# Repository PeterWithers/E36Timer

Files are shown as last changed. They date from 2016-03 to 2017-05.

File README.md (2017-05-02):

# E36Timer
Simple and cheep free flight timer

This timer is based on the attiny86 usb board. These boards usually ship with the micronucleus boot loader, in which case it can be flashed with the command line tool: micronucleus --run e36timer.hex

The components required for this are: attiny86 usb board, push button and wiring for the button, servo and ESC.

When the device is powered up there will be a period of time in which the motor run time and DT time can be adjusted. The options will be: 
Motor times: 5, 10, 15 seconds
DT time: 0, 5, 30, 60, 90, 120, 180, 240, 300 seconds

It is possible that powersupply noise or interruptions could cause the attiny to brownout. For this reason the first action on power up should be to release the DT, otherwise a brownout mid flight could prevent or delay DT.

The main working branch for this project is now on GITLAB during the current stage of development.

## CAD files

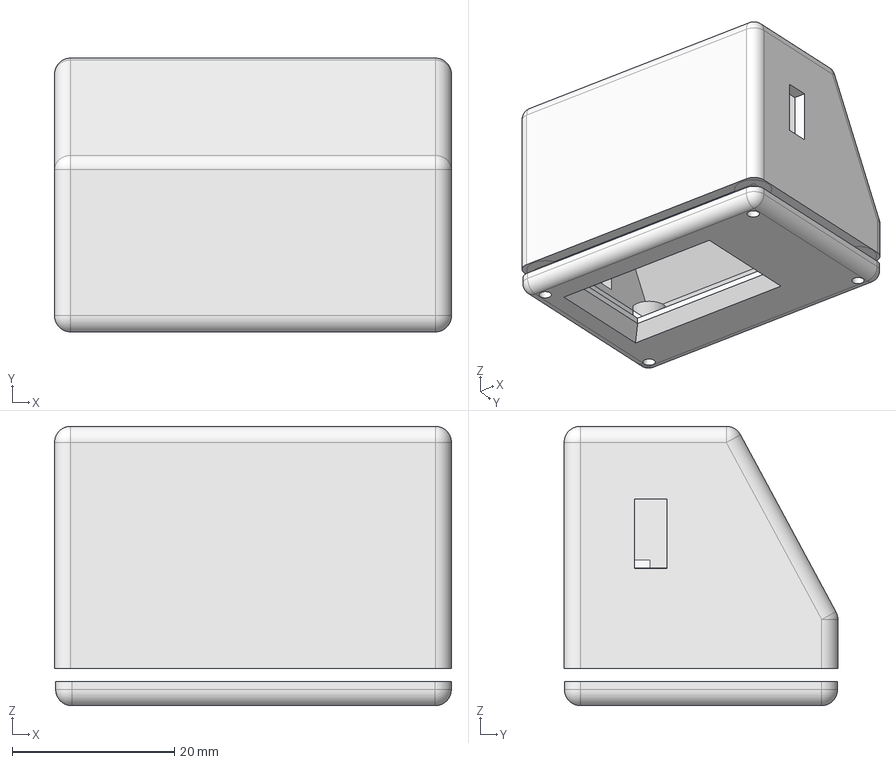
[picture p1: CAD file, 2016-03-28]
timer_testing_tool/testing_tool_case.FCStd
49.0 x 33.8 x 34.5 mm
LCD
Board
USB
Connector

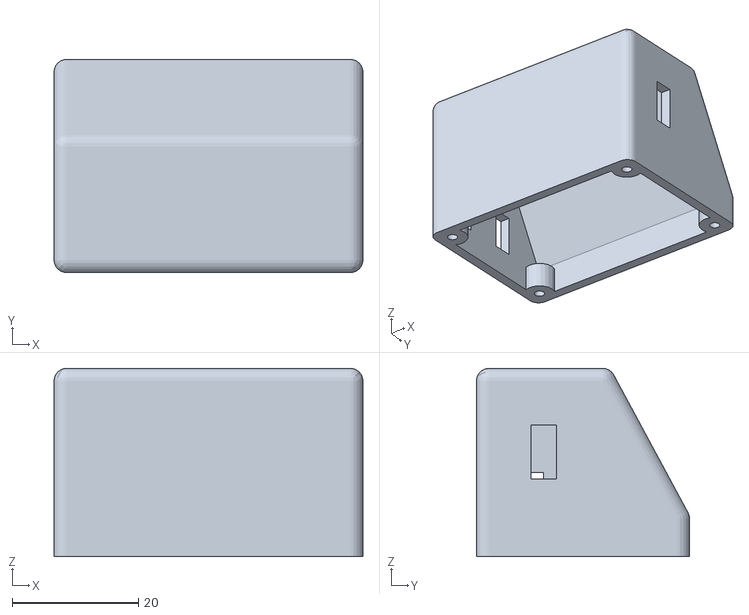
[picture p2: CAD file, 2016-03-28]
timer_testing_tool/case_body.stl
49.0 x 33.8 x 29.9

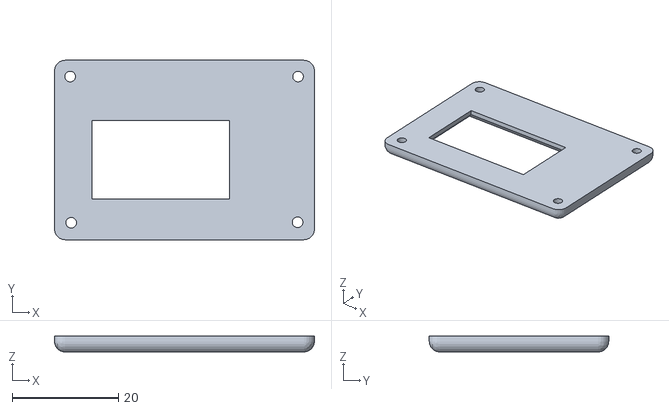
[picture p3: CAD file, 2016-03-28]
timer_testing_tool/face_plate.stl
48.8 x 33.7 x 3.00

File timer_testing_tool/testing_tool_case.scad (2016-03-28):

/*
 * Copyright (C) 2016 Peter Withers
 */

/*
 * testing_tool_case.scad
 *
 * Created: 21/03/2016 23:18
 * Author : Peter Withers <peter@gthb-bambooradical.com>
 */

lcdHoleSpacing = 23;
lcdBoardWidth = 28; // the board is square
lcdDisplayHeight = 18; // the lcd is as wide as the board

atmegaBoardWidth = 18;
atmegaBoardLength = 43;

gapBetweenBoardEdgeAndLcd = 5;

usbWidth = 8;
usbHeight = 4;

//translate([0,5,5]) %cube([atmegaBoardLength, 30, lcdBoardWidth+5], center = true);
//cube([atmegaBoardLength, atmegaBoardWidth, 3], center = true);
//translate([-5,18,5]) cube([lcdBoardWidth, 3, lcdBoardWidth], center = true);
//translate([-5,20,4]) cube([lcdBoardWidth, 5, lcdDisplayHeight], center = true);
//translate([25,0,-3]) cube([usbWidth, usbWidth, usbHeight], center = true);
//translate([-25,0,-3]) rotate(90, [0,1,0]) cylinder(r = 3, h = 10, center = true);

difference() {
	// facePlate
	translate([0,22,5]) cube([atmegaBoardLength+ 5, 3, lcdBoardWidth+5], center = true);
	// LCD hole
	translate([-5,20,4]) cube([lcdBoardWidth, 15, lcdDisplayHeight], center = true);
	rotate(90, [0,1,0]) translate([-5,20,4]) cylinder(r=1,h=30, center = true);
	
}

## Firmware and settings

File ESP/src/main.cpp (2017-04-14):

/*
 * Copyright (C) 2016 Peter Withers
 */

/*
 * E36Timer.c
 *
 * Created: 13/02/2016 18:00:32
 * Author : Peter Withers <peter@gthb-bambooradical.com>
 */

//#include <Arduino.h>
//#include <eeprom.h>
#include <EEPROM.h>
#include <Servo.h>
// todo: this include and related defines are temporary
//#include <NewPing.h>
#include <user_interface.h>
#include <ESP8266WiFi.h>
#include <DNSServer.h>
#include <ESP8266WebServer.h>
#include <ESP8266HTTPUpdateServer.h>
#include <Sodaq_BMP085.h>
#include <Wire.h>
#include <Ticker.h>

Ticker pwmTweenTimer;
ADC_MODE(ADC_VCC);
WiFiUDP Udp;
unsigned int localUdpPort = 2222;

const byte DNS_PORT = 53;
IPAddress timerIP(192, 168, 1, 1);
IPAddress remoteIP(192, 168, 1, 2);
DNSServer dnsServer;
ESP8266WebServer webServer(80);
ESP8266HTTPUpdateServer httpUpdater;

Sodaq_BMP085 pressureSensor;
double baselinePressure;
bool isTimer = false;
bool hasPressureSensor = true;

int historyLength = 1024;
int historyIndex = 0;
int udpHistoryIndex = 0;
int flightStartIndex = 0;
float temperatureHistory[1024];
float altitudeHistory[1024];
uint8_t escHistory[1024];
uint8_t dtHistory[1024];
int32_t remoteRssiHistory[1024];
float remoteVoltageHistory[1024];
int maxSvgValue = 0;

//#define TRIGGER_PIN  3
//#define ECHO_PIN     2
//#define MAX_DISTANCE 400

//NewPing sonar(TRIGGER_PIN, ECHO_PIN, MAX_DISTANCE);
// end temporary defines

#define IndicatorLed     2
#define ServoPWM         4
#define EscPWM           5
#define ButtonPin        0
#define SdaPin           12
#define SclPin           14

Servo dtServo;
Servo escServo;

#define MaxPwm 141
#define MinPwm 44

//#define ButtonIsDown (sonar.ping_cm() < 30)
#define ButtonIsDown (digitalRead(ButtonPin) == 0)
#define RcDtIsActive false
//#define RcDtIsActive (digitalRead(RcDt1Pin) == 0)

#define TurnOnLed digitalWrite(IndicatorLed, 1)
#define TurnOffLed digitalWrite(IndicatorLed, 0)

typedef union {

    struct {
        uint8_t dtStatus;
        int32_t rssi;
        uint16_t voltage;
    } data;
    uint8_t asBytes[sizeof (data)];
} TelemetryData;

enum MachineState {
    setupSystem,
    throttleMax,
    waitingButtonRelease1,
    throttleMin,
    waitingButtonRelease2,
    startWipe1, // when the device resets we wipe the servo arm to release the DT lever so that a reset in midair does not prevent DT
    endWipe1,
    editMotorTime,
    startWipe2, // between the settings wipe to indicate the change
    endWipe2,
    editDtTime,
    saveEepromSettings,
    waitingButtonStart,
    clearGraphArrays,
    waitingButtonRelease,
    motorRun,
    freeFlight,
    triggerDT,
    waitingForRestart,
    waitingFirmwareUpdate,
    dtRemoteConfig,
    dtRemote
};

volatile enum MachineState machineState = setupSystem;

volatile unsigned long buttonLastChangeMs = 0;
volatile unsigned long buttonDebounceMs = 100;

volatile unsigned long lastMotorSpinUpMs = 0;
volatile unsigned long flightIdRandom1 = 0;
volatile unsigned long flightIdRandom2 = 0;
volatile unsigned long currentFlightMs = 0;
volatile unsigned long lastStateChangeMs = 0;
volatile const unsigned long editingTimeoutMs = 3000;
volatile const unsigned long escSpinDownMs = 1000;
volatile const unsigned long escSpinUpMs = 1000;
volatile const unsigned long servoWipeMs = 1000;
volatile const unsigned long displayStepMs = 500;
volatile unsigned long editingStartMs = 0;
volatile const unsigned long powerDownServoMs = 30l * 1000l; // 30 seconds before the servo is powered down
volatile const unsigned long powerDownEscSeconds = 300l * 1000l; // 5 minutes before the ESC is powered down

const unsigned long motorSeconds[] = {2, 4, 5, 7, 10, 13, 15};
const int motorSecondsSize = 6;
volatile int motorSecondsIndex = 0;
const unsigned long dethermalSeconds[] = {0, 5, 30, 60, 90, 120, 180, 240, 300};

// start measured actual times
// tested with the timer calibrated to produce 50.38hz
// motor 2: {2.3}
// motor 7: {7.2}
// motor 15: {14.9,14.6,14.9,14.7};
// any DT below motor time of 15: {16.0,15.7}
// DT 0 with motor 2: {3.4}
// DT 30: {30.6};
// DT 60: {59.8};
// DT 300: {293.0};
// end measured actual times

const int dethermalSecondsSize = 9;
volatile int dethermalSecondsIndex = 0;
const int waitingEscValue = ((MaxPwm - MinPwm) / 3) + MinPwm;
volatile int buttonHasBeenUp = 0;

char ssid[32] = "";
char password[32] = "";

void slowFlash() {
    if (millis() / 1000 % 2 == 0) {
        TurnOnLed;
    } else {
        TurnOffLed;
    }
}

void fastFlash() {
    if ((millis() / (1000 / 5)) % 2 == 0) {
        TurnOnLed;
    } else {
        TurnOffLed;
    }
}

void doubleFlash() {
    int pulseIndex = (millis() / (1000 / 5)) % 10;
    if (pulseIndex == 0 || pulseIndex == 3) {
        TurnOnLed;
    } else {
        TurnOffLed;
    }
}

void trippleFlash() {
    int pulseIndex = (millis() / (1000 / 5)) % 10;
    if (pulseIndex == 0 || pulseIndex == 2 || pulseIndex == 4) {
        TurnOnLed;
    } else {
        TurnOffLed;
    }
}

void setCredentials() {
    if (webServer.hasArg("ssid") && webServer.hasArg("pass")) {
        webServer.arg("ssid").toCharArray(ssid, sizeof (ssid) - 1);
        webServer.arg("pass").toCharArray(password, sizeof (password) - 1);
        EEPROM.begin(512);
        EEPROM.put(9, ssid);
        EEPROM.put(9 + sizeof (ssid), password);
        char ok[2 + 1] = "OK";
        EEPROM.put(9 + sizeof (ssid) + sizeof (password), ok);
        EEPROM.commit();
        EEPROM.end();
    }
}

void saveSettings() {
    boolean changeMade = false;
    EEPROM.begin(512);
    Serial.print(" motorSecondsIndex: ");
    Serial.print(motorSecondsIndex);
    Serial.print(" EEPROM.read(1): ");
    Serial.print(EEPROM.read(1));
    // using update not write to preserve eeprom life
    // update does not seem to exist in the ESP library so we test before setting to preserve the eeprom
    if (EEPROM.read(1) != motorSecondsIndex) {
        Serial.print(" motorSecondsIndex storing changes");
        EEPROM.write(1, motorSecondsIndex);
        changeMade = true;
    } else {
        Serial.print(" motorSecondsIndex unchanged");
    }
    if (EEPROM.read(2) != dethermalSecondsIndex) {
        Serial.print(" dethermalSecondsIndex storing changes");
        EEPROM.write(2, dethermalSecondsIndex);
        changeMade = true;
    } else {
        Serial.print(" dethermalSecondsIndex unchanged");
    }
    byte settingsByte = EEPROM.read(3);
    if (bitRead(settingsByte, 0) != isTimer || bitRead(settingsByte, 1) != hasPressureSensor) {
        Serial.print(" toggleTimerOrRemote, hasPressureSensor storing changes");
        bitWrite(settingsByte, 0, isTimer);
        bitWrite(settingsByte, 1, hasPressureSensor);
        EEPROM.write(3, settingsByte);
        changeMade = true;
    } else {
        Serial.print(" toggleTimerOrRemote, hasPressureSensor unchanged");
    }
    if (changeMade) {
        Serial.print(" writing changes");
        EEPROM.commit();
    } else {
        Serial.print(" unchanged no commit");
    }
    EEPROM.end();
}

void loadSavedSettings() {
    EEPROM.begin(512);
    motorSecondsIndex = EEPROM.read(1);
    dethermalSecondsIndex = EEPROM.read(2);
    byte settingsByte = EEPROM.read(3);
    isTimer = bitRead(settingsByte, 0);
    hasPressureSensor = bitRead(settingsByte, 1);
    motorSecondsIndex = (motorSecondsIndex < motorSecondsSize) ? motorSecondsIndex : motorSecondsSize - 1;
    dethermalSecondsIndex = (dethermalSecondsIndex < dethermalSecondsSize) ? dethermalSecondsIndex : dethermalSecondsSize - 1;
    EEPROM.get(9, ssid);
    EEPROM.get(9 + sizeof (ssid), password);
    char ok[2 + 1];
    EEPROM.get(9 + sizeof (ssid) + sizeof (password), ok);
    if (String(ok) != String("OK")) {
        ssid[0] = 0;
        password[0] = 0;
    }
    EEPROM.end();
}

void pinChangeInterrupt() {
    buttonLastChangeMs = millis();
}

String getTelemetryJson() {
    String returnString = "machineState: '";
    switch (machineState) {
        case setupSystem:
            returnString += "setupSystem";
            break;
        case throttleMax:
            returnString += "throttleMax";
            break;
        case waitingButtonRelease1:
            returnString += "waitingButtonRelease1";
            break;
        case throttleMin:
            returnString += "throttleMin";
            break;
        case waitingButtonRelease2:
            returnString += "waitingButtonRelease2";
            break;
        case startWipe1:
            returnString += "startWipe1";
            break;
        case endWipe1:
            returnString += "endWipe1";
            break;
        case editMotorTime:
            returnString += "editMotorTime";
            break;
        case startWipe2:
            returnString += "startWipe2";
            break;
        case endWipe2:
            returnString += "endWipe2";
            break;
        case editDtTime:
            returnString += "editDtTime";
            break;
        case saveEepromSettings:
            returnString += "saveEepromSettings";
            break;
        case waitingButtonStart:
            returnString += "waitingButtonStart";
            break;
        case clearGraphArrays:
            returnString += "clearGraphArrays";
            break;
        case waitingButtonRelease:
            returnString += "waitingButtonRelease";
            break;
        case motorRun:
            returnString += "motorRun";
            break;
        case freeFlight:
            returnString += "freeFlight";
            break;
        case triggerDT:
            returnString += "triggerDT";
            break;
        case waitingForRestart:
            returnString += "waitingForRestart";
            break;
        case waitingFirmwareUpdate:
            returnString += "waitingFirmwareUpdate";
            break;
        case dtRemoteConfig:
            returnString += "dtRemoteConfig";
            break;
        case dtRemote:
            returnString += "dtRemote";
            break;
    }
    int servoPosition = dtServo.read();
    int escPosition = escServo.read();
    returnString += "'; servoPosition: ";
    returnString += servoPosition;
    returnString += "; escPosition: ";
    returnString += escPosition;
    returnString += "; dethermalSeconds: ";
    returnString += dethermalSeconds[dethermalSecondsIndex];
    returnString += "; motorSeconds: ";
    returnString += motorSeconds[motorSecondsIndex];
    returnString += "; rssi: ";
    returnString += WiFi.RSSI();
    returnString += "; lastStateChangeMs: ";
    returnString += (millis() - lastStateChangeMs);
    return returnString;
}

bool getPressure(double &temperature, double &pressure, double &altitude) {
    temperature = pressureSensor.readTemperature();
    pressure = pressureSensor.readPressure();
    altitude = pressureSensor.readAltitude(baselinePressure);

    /*Serial.print("altitudeHistory: ");
    for (int currentIndex = 0; currentIndex < historyLength; currentIndex++) {
        Serial.print(altitudeHistory[currentIndex]);
        Serial.print(", ");
    }
    Serial.println(";");
    Serial.print("temperatureHistory: ");
    for (int currentIndex = 0; currentIndex < historyLength; currentIndex++) {
        Serial.print(temperatureHistory[currentIndex]);
        Serial.print(", ");
    }
    Serial.println(";");*/
    return true;
}
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
void loop() {
    switch (machineState) {
        case saveEepromSettings:
            saveSettings();
            machineState = waitingButtonStart;
            break;
        case clearGraphArrays:
            machineState = waitingButtonRelease;
            // zero the historyIndex and zero the history buffer
            lastMotorSpinUpMs = millis();
            flightIdRandom1 = random(1000, 9999); // @todo: the random seed has not been set, check that this will not cause issues in this use case.
            flightIdRandom2 = random(1000, 9999);
            memset(temperatureHistory, 0, sizeof (temperatureHistory));
            memset(altitudeHistory, 0, sizeof (altitudeHistory));
            memset(escHistory, 0, sizeof (escHistory));
            memset(dtHistory, 0, sizeof (dtHistory));
            memset(remoteRssiHistory, 0, sizeof (remoteRssiHistory));
            memset(remoteVoltageHistory, 0, sizeof (remoteVoltageHistory));
            break;
        case dtRemoteConfig:
            if (WiFi.status() == WL_CONNECTED) {
                dnsServer.stop();
                webServer.stop();
                WiFi.softAPdisconnect(true);
                WiFi.mode(WIFI_STA);
                machineState = dtRemote;
            }
            break;
        case dtRemote:
            TelemetryData telemetryData;
            if (ButtonIsDown) {
                telemetryData.data.dtStatus = 'd';
                Udp.beginPacket(timerIP, localUdpPort);
                Udp.write(telemetryData.asBytes, sizeof (telemetryData));
                Udp.endPacket();
            } else {
                int currentIndex = ((millis() - lastMotorSpinUpMs) / 1000);
                if (currentIndex != udpHistoryIndex) {
                    telemetryData.data.dtStatus = 'r';
                    telemetryData.data.rssi = WiFi.RSSI();
                    telemetryData.data.voltage = ESP.getVcc();
                    //                    Serial.print("rssi: ");
                    //                    Serial.println(telemetryData.data.rssi);
                    //                    Serial.print("voltage: ");
                    //                    Serial.println(telemetryData.data.voltage);
                    udpHistoryIndex = currentIndex;
                    Udp.beginPacket(timerIP, localUdpPort);
                    Udp.write(telemetryData.asBytes, sizeof (telemetryData));
                    Udp.endPacket();
                }
            }
            int packetSize = Udp.parsePacket();
            if (packetSize) {
                //                Serial.print("Found packet");
                Udp.flush();
            }
            break;
    }
    if (machineState == dtRemoteConfig) {
        dnsServer.processNextRequest();
        webServer.handleClient();
    } else if (machineState != dtRemote) {
        updateHistory();
        bool foundDtPacket = checkDtPacket();
        if (foundDtPacket || RcDtIsActive) { // respond to an RC DT trigger regardless of the machine state
            machineState = triggerDT;
            lastStateChangeMs = millis();
        } else {
            dnsServer.processNextRequest();
            webServer.handleClient();
        }
    }
    yield();
}

void setupRegisters() {
    pinMode(IndicatorLed, OUTPUT); // set the LED to output
    pinMode(ButtonPin, INPUT); // set the button to input
    pinMode(ButtonPin, INPUT_PULLUP); // activate the internal pull up resistor
    attachInterrupt(ButtonPin, pinChangeInterrupt, CHANGE);
    //    powerUp();
    dtServo.write(MinPwm); // set the servo to the minimum for now
    escServo.write(MinPwm); // set the ESC to the minimum for now
    pinMode(A0, INPUT);
}

void getTelemetry() {
    //    Serial.print("getTelemetry");
    webServer.send(200, "text/html", getTelemetryString());
}

void getSettingsJson() {
    String returnSettinsJson = "{";
    returnSettinsJson += "\"settings\": [{\
    \"index\": ";
    returnSettinsJson += dethermalSecondsIndex;
    returnSettinsJson += ",\
            \"value\": ";
    returnSettinsJson += dethermalSeconds[dethermalSecondsIndex];
    returnSettinsJson += ",\
            \"values\": [0, 5, 30, 60, 90, 120, 180, 240, 300],\
            \"description\": \"Dethermal Seconds\",\
            \"name\": \"dethermalSeconds\",\
            \"links\": [{\
                    \"rel\": \"+\",\
                    \"href\": \"dtIncrease\"\
                }, {\
                    \"rel\": \"-\",\
                    \"href\": \"dtDecrease\"\
                }]\
        }, {\
            \"index\": ";
    returnSettinsJson += motorSecondsIndex;
    returnSettinsJson += ",\
            \"value\": ";
    returnSettinsJson += motorSeconds[motorSecondsIndex];
    returnSettinsJson += ",\
            \"description\": \"Motor Seconds\",\
            \"name\": \"motorSeconds\",\
            \"values\": [2, 4, 5, 7, 10, 13, 15],\
            \"links\": [{\
                    \"rel\": \"+\",\
                    \"href\": \"motorIncrease\"\
                }, {\
                    \"rel\": \"-\",\
                    \"href\": \"motorDecrease\"\
                }]\
        }, {\
            \"integer\": 30,\
            \"description\": \"Power Down Servo Seconds\",\
            \"name\": \"powerDownServoMs\",\
            \"links\": [{\
                    \"rel\": \"self\",\
                    \"href\": \"powerDownServoMs\"\
                }]\
        }, {\
            \"integer\": 300000,\
            \"description\": \"Power Down ESC Seconds\",\
            \"name\": \"powerDownEscSeconds\",\
            \"links\": [{\
                    \"rel\": \"self\",\
                    \"href\": \"powerDownEscSeconds\"\
                }]\
        }, {\
            \"boolean\": true,\
            \"description\": \"Pressure Sensor\",\
            \"name\": \"pressureSensor\",\
            \"links\": [{\
                    \"rel\": \"self\",\
                    \"href\": \"toggleSensors\"\
                }]\
        }, {\
            \"boolean\": true,\
            \"description\": \"Timer or Remote\",\
            \"name\": \"isTimer\",\
            \"links\": [{\
                    \"rel\": \"self\",\
                    \"href\": \"toggleTimerOrRemote\"\
                }]\
        }],\
    \"links\": [{\
            \"rel\": \"self\",\
            \"href\": \"settings\"\
        }]\
}   ";
    webServer.send(200, "text/html", returnSettinsJson);
}

//        webServer.on("/dethermalSeconds", HTTP_PUT, putDethermalSeconds);
//        webServer.on("/motorSeconds", HTTP_PUT, putMotorSeconds);
//        webServer.on("/powerDownServoMs", HTTP_PUT, putPowerDownServoMs);
//        webServer.on("/powerDownEscSeconds", HTTP_PUT, putPowerDownEscSeconds);
//        webServer.on("/hasPressureSensor", HTTP_PUT, putHasPressureSensor);
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

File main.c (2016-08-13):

/*
 * Copyright (C) 2016 Peter Withers
 */

/*
 * E36Timer.c
 *
 * Created: 13/02/2016 18:00:32
 * Author : Peter Withers <peter@gthb-bambooradical.com>
 */

#include <avr/io.h>
#include <avr/interrupt.h>
#include <avr/eeprom.h>

#define IndicatorLed     PB1
#define ServoPWM         PB0
#define EscPWM           PB4
#define ButtonPin        PB2
#define RcDt1Pin         PB3 // on the attiny85 board the D- pin is pulled high by a 1k5 resistor and therefore should not trigger when no radio module is installed
#define RcDt2Pin         PB5

#define MaxOCR0A 129
#define MinOCR0A 64
//#define MaxOCR0A 140
//#define MinOCR0A 50

#define ButtonIsDown ((PINB & (1 << ButtonPin)) == 0)
#define RcDtIsActive ((PINB & (1 << RcDt1Pin)) == 0)

#define TurnOnLed PORTB |= (1 << IndicatorLed);
#define TurnOffLed PORTB &= ~(1 << IndicatorLed);

enum MachineState {
    setupSystem,
    throttleMax,
    waitingButtonRelease1,
    throttleMin,
    waitingButtonRelease2,
    startWipe1, // when the device resets we wipe the servo arm to release the DT lever so that a reset in midair does not prevent DT
    endWipe1,
    editMotorTime,
    startWipe2, // between the settings wipe to indicate the change
    endWipe2,
    editDtTime,
    waitingButtonStart,
    waitingButtonRelease,
    motorRun,
    freeFlight,
    triggerDT,
    waitingForRestart
};

volatile enum MachineState machineState = setupSystem;

volatile int buttonCountSinceLastChange = 0;
volatile int buttonDebounceValue = 3;
volatile int pwmCycleCount = 0;

volatile const int editingTimeoutSeconds = 3;
volatile int editingTimeoutCount;
volatile const int powerDownServoSeconds = 30; // 30 seconds before the servo is powered down
volatile const int powerDownEscSeconds = 300; // 5 minutes before the ESC is powered down 
volatile const int cyclesPerSecond = 49;

const int motorSeconds[] = {2, 4, 5, 7, 10, 13, 15};
const int motorSecondsSize = 6;
volatile uint8_t motorSecondsIndex = 0;
const int dethermalSeconds[] = {0, 5, 30, 60, 90, 120, 180, 240, 300};

// start measured actual times
// tested with the timer calibrated to produce 50.38hz
// motor 2: {2.3}
// motor 7: {7.2}
// motor 15: {14.9,14.6,14.9,14.7};
// any DT below motor time of 15: {16.0,15.7}
// DT 0 with motor 2: {3.4}
// DT 30: {30.6};
// DT 60: {59.8};
// DT 300: {293.0};
// end measured actual times

const int dethermalSecondsSize = 9;
volatile uint8_t dethermalSecondsIndex = 0;
volatile int timer0OverflowCounter = 0;
const int waitingEscValue = ((MaxOCR0A - MinOCR0A) / 3) + MinOCR0A;
volatile int buttonHasBeenUp = 0;

void slowFlash(int pwmCycleCount) {
    if (pwmCycleCount / cyclesPerSecond % 2 == 0) {
        TurnOnLed;
    } else {
        TurnOffLed;
    }
}

void fastFlash(int pwmCycleCount) {
    if ((pwmCycleCount / (cyclesPerSecond / 5)) % 2 == 0) {
        TurnOnLed;
    } else {
        TurnOffLed;
    }
}

void doubleFlash(int pwmCycleCount) {
    int pulseIndex = (pwmCycleCount / (cyclesPerSecond / 5)) % 10;
    if (pulseIndex == 0 || pulseIndex == 3) {
        TurnOnLed;
    } else {
        TurnOffLed;
    }
}

void trippleFlash(int pwmCycleCount) {
    int pulseIndex = (pwmCycleCount / (cyclesPerSecond / 5)) % 10;
    if (pulseIndex == 0 || pulseIndex == 2 || pulseIndex == 4) {
        TurnOnLed;
    } else {
        TurnOffLed;
    }
}

void saveSettings() {
    // using update not write to preserve eeprom life
    eeprom_update_byte((uint8_t*) 1, motorSecondsIndex);
    eeprom_update_byte((uint8_t*) 2, dethermalSecondsIndex);
}

void loadSavedSettings() {
    motorSecondsIndex = eeprom_read_byte((uint8_t*) 1);
    dethermalSecondsIndex = eeprom_read_byte((uint8_t*) 2);
    motorSecondsIndex = (motorSecondsIndex < motorSecondsSize) ? motorSecondsIndex : motorSecondsSize - 1;
    dethermalSecondsIndex = (dethermalSecondsIndex < dethermalSecondsSize) ? dethermalSecondsIndex : dethermalSecondsSize - 1;

    // if the osccalSavedIndicator value is not found then assume this is the first run after loading the firmware
    // after the firmware has been flashed the OSCCAL value will have been set by the boot loader so we save this to the EEPROM
    // on all other boots we set OSCCAL from the previously saved value from the EEPROM
    uint8_t osccalSavedIndicator = eeprom_read_byte((uint8_t*) 5);
    int osccalSavedIndex = 19;
    if (osccalSavedIndicator == osccalSavedIndex) {
        OSCCAL = eeprom_read_byte((uint8_t*) 6);
    } else {
        eeprom_update_byte((uint8_t*) 6, OSCCAL);
        eeprom_update_byte((uint8_t*) 5, osccalSavedIndex);
    }
}

ISR(PCINT0_vect) {
    buttonCountSinceLastChange = 0;
}

void updateStartWipe(enum MachineState completionState) {
    OCR0A = (OCR0A + 2 < MaxOCR0A) ? OCR0A + 2 : MaxOCR0A;
    if (OCR0A >= MaxOCR0A) {
        machineState = completionState;
        pwmCycleCount = 0;
    }
}

void updateEndWipe(enum MachineState completionState) {
    OCR0A = (OCR0A - 2 > MinOCR0A) ? OCR0A - 2 : MinOCR0A;
    if (OCR0A <= MinOCR0A) {
        machineState = completionState;
        pwmCycleCount = 0;
        editingTimeoutCount = editingTimeoutSeconds * cyclesPerSecond;
    }
}

void displayMotorTime(int pwmCycleCount) {
    // show the steps / divisions before resting at the selected value
    if ((pwmCycleCount / 20) <= motorSecondsIndex) {
        uint8_t stepValue = MinOCR0A + ((MaxOCR0A - MinOCR0A) * (pwmCycleCount / 20) / (motorSecondsSize - 1));
        editingTimeoutCount = pwmCycleCount + (editingTimeoutSeconds * cyclesPerSecond);
        OCR0A = stepValue;
    } else {
        uint8_t displayValue = MinOCR0A + ((MaxOCR0A - MinOCR0A) * motorSecondsIndex / (motorSecondsSize - 1));
        OCR0A = displayValue;
    }
}

void displayDethermalTime(int pwmCycleCount) {
    // show the steps / divisions before resting at the selected value
    if ((pwmCycleCount / 20) <= dethermalSecondsIndex) {
        uint8_t stepValue = MinOCR0A + ((MaxOCR0A - MinOCR0A) * (pwmCycleCount / 20) / (dethermalSecondsSize - 1));
        editingTimeoutCount = pwmCycleCount + (editingTimeoutSeconds * cyclesPerSecond);
        OCR0A = stepValue;
    } else {
        uint8_t displayValue = MinOCR0A + ((MaxOCR0A - MinOCR0A) * dethermalSecondsIndex / (dethermalSecondsSize - 1));
        OCR0A = displayValue;
    }
}

void powerUp() {
    DDRB |= 1 << ServoPWM; // enable the servo output
    DDRB |= 1 << EscPWM; // enable the ESC output
}

void checkPowerDown(int pwmCycleCount) {
    if (pwmCycleCount > powerDownServoSeconds * cyclesPerSecond) {
        // power down the servo after the given delay
        DDRB &= ~(1 << ServoPWM); // disable the servo output
    }
    if (pwmCycleCount > powerDownEscSeconds * cyclesPerSecond) {
        // power down the ESC after the given delay
        DDRB &= ~(1 << EscPWM); // disable the ESC output
    }
}
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

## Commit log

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2016-02-14 Added states for start wipe and end wipe. Added ESC PWM based on the difference between compare registers A and B to avoid an issue with the simulator and the overflow ISR.
    [main.c]
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2016-02-17 Added more LED state indicators and timeouts for editing the motor run and DT settings.
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2016-02-19 Added use of the timer0 overflow interrupt. Increased the timer0 frequency and manually set the GPIO on some of the overflows so that the PWM for 1 - 2 ms can be much more accurate. Added more deboun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
2016-02-19 Added correct syntax for EEPROM access, although it is not used yet.
    [main.c]
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2016-02-20 Tweaked the timer prescaler and cycle actions so that a nice 50hz and 10%-20% duty cycle is produced.
2016-02-20 Corrected the duty cycle max and min values.
    [main.c]
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2016-02-20 Added restarts from motor run state to waiting for release state by button push.
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2016-02-20 Added more debounce code so that the button must be up or down before the next state action can occur. Added value capping to the settings loaded from eeprom, so that on first run only valid values c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
2016-03-19 Added logic to detect the first run and save the calibrated OSCCAL value to EEPROM. This saved value is placed back into the OSCCAL from the EEPROM on all other boots. Halved the edit settings timeou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
2016-03-21 Started a timer testing tool using an atmega and i2c lcd screen.
2016-03-21 Corrected the millis divider value.
    [timer_testing_tool.cpp]
2016-03-21 Added an scad file of a case for the boards.
    [testing_tool_case.scad]
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2016-03-24 FInished debugging and now have clear timing data for the PWM duty cycle.
2016-03-24 Tidied up code after the debugging. The frequency in hertz and duty cycle of the PWM is now displayed on the LCD.
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2016-03-25 Tweaked the minimum ESC percent before counting time, to prevent held button time being included.
    [timer_testing_tool.cpp]
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2016-03-25 Tweaked the min and max PWM values required by the oscillator calibration.
    [main.c]
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2016-03-25 Tweaked the editing timeout to 3seconds. Left the ESC powered down until this point because some ESCs have timing issues that the bootloader delay seems to affect.
    [main.c]
2016-03-25 Resolved the screen tearing issue. Set the servo PWM signal as the base for the frequency calculation.
    [timer_testing_tool.cpp]
2016-03-25 Modified the DT timer to display as soon as the motor run starts. Addressed an issue that caused the DT timer to stop counting if a miss read of the PWM occurred.
    [timer_testing_tool.cpp]
2016-03-26 Addressed an issue that caused the DT timer to stop counting if a miss read of the PWM occurred.
    [timer_testing_tool.cpp]
2016-03-26 Addressed an issue that caused the DT timer to stop counting.
    [timer_testing_tool.cpp]
2016-03-28 Designed a case for the device and added the STL and FreeCAD files.
    [case_body.stl, face_plate.stl, testing_tool_case.FCStd]
2016-03-28 Last changes to the OpenSCAD file which has been replaced by a FreeCAD version.
    [testing_tool_case.scad]
2016-03-28 Started testing the actual timer output against the expected motor and dt times and put the results in as comments. Corrected the DT time so that it overlaps the motor time.
    [main.c]
2016-03-28 Tweaked the timer calibration / cycles per second. Corrected the inclusion of the motor time into the DT time.
    [main.c]
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2016-05-18 Added a connection diagram of the attiny85 and the ESC, servo and switch.
2016-05-22 Added an indication of the connection from the switch to 0v in the connection diagram.
2016-05-29 Started a new firmware file that will be used to program the ESC via the timer.
2016-05-29 First version firmware which can be used to program the ESC via the timer.
2016-05-29 Modified the edit setting stage to make it clear which item is being edited, by adding a the servo wipe between the edit motor time and the edit DT time. Added a power down state when 30 seconds of i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
2016-05-29 Added power down to both the waitingButtonStart and the waitingForRestart states. Added to separate power down times, 30 seconds for the servo and 5 minutes for the ESC.
2016-05-29 Added steps to the servo movement when indicating the current setting so that it is easier to identify the current value on start up.
2016-06-04 Added a usage diagram indicating the motor and DT values available during start up.
2016-07-28 Added a DT trigger via a negative voltage on PB3 for use with a radio module to provide RC DT.
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2016-08-13 Updated the settings digram to show the motor time of 13 seconds. Added the DT connection to the connections diagram. Corrected a syntactic error in the program.
    [main.c]
2016-08-14 Started an experimental version of the timer based on esp12e and esp07 boards.
2016-08-14 Started a CPP experimental version of the timer based on esp12e and esp07 boards.
2016-08-14 Migrated the timer code to platform agnostic libraries rather than low level timer mechanisms in preparation for the esp12e and esp07 boards.
2016-08-21 Changed the timing paradigm to better suit the platform agnostic libraries rather than low level timer mechanisms.
2016-11-06 Corrected the motor power down phase. Started to add barometric sensor features.
    [main.cpp]
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2016-11-15 Added separate DT remote and timer functions based on compile time option. Added use of UDP packets sent from the DT remote to the timer.
2016-11-16 Prevented delays sending the TD trigger over UDP. Added RSSI to the telemetry output.
    [main.cpp]
2017-03-05 Added the BMP180 pressure sensor. Tweaked the button pin to match the board. Configured the SDA and SCL pins to suit the available pins
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2017-03-05 Swapped the BMP180 pressure sensor library for one that works on ESP.
    [main.cpp]
2017-03-05 Set the baseline pressure when taking readings. Added arrays for temperature and pressure history data. Added a http endpoint to retrieve the history data in JSON format.
2017-03-11 Changed time variables from int to long. Corrected some local variable names.
    [main.cpp]
2017-03-11 Added DT and ESC to the stored history. Added a SVG graph output and html link to it.
2017-03-11 Corrected a string error.
    [main.cpp]
2017-03-11 Added graph colours and inverted the graph lines.
    [main.cpp]
2017-03-25 Added flight graph data loading. Added a handler to periodically check the wifi and status of the flight timer.
2017-03-25 Added dt and esc states in the graph. Added internal storage of saved graphs.
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2017-03-29 Changed the ESC and servo output pins. Added RSSI to the telemetry json.
2017-03-29 Added a link to disable the sensor reading in the main loop.
2017-04-02 Started to implement requesting the specific wifi network for timer HTTP connections.
2017-04-02 Utilised the json data paging added to the timer HTTP telemetry request.
2017-04-03 Added a JSON file of settings to be provided by the timer.
2017-04-03 Added a ticker to tween the PWM output outside of the main loop. Added a settings JSON HTTP endpoint.
2017-04-04 Changed the saved flight data location to the external storage. Changed network access method so that the timer can be accessed over wifi while a mobile network is active.
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2017-04-04 Changed the file name generation to use 24 hour time. Tweaked the graph updating to address the graph not updating when the length is shorter than the current.
2017-04-05 Removed the RMS array since it is of no use. Added loading of the settings JSON from the timer.
2017-04-07 Added a title to the graph and labels for the motor and dt settings.
2017-04-07 Added a title to the graph and labels for the motor and dt settings. Allowed the graph data thread to get data from the timer at a reduced rate when the device screen is off.
2017-04-07 Added EEPROM storage of the SSID and the device type (timer or remote).
2017-04-07 Changed the circular buffer so that the mobile app knows the total history length not just the current buffer length. Prevented the return of history data that under runs the buffer length. Added the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
    [main.cpp]
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2017-04-08 Corrected the current flight seconds to the graph screen. Added labels to the graph every 10 seconds.
    [main.cpp]
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2017-04-14 Added handling of WDT resets in the case of a timer that does not have a BMP180 but is told to get pressure readings.
    [main.cpp]
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
